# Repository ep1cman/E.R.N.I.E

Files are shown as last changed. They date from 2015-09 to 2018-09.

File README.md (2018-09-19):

About
=====

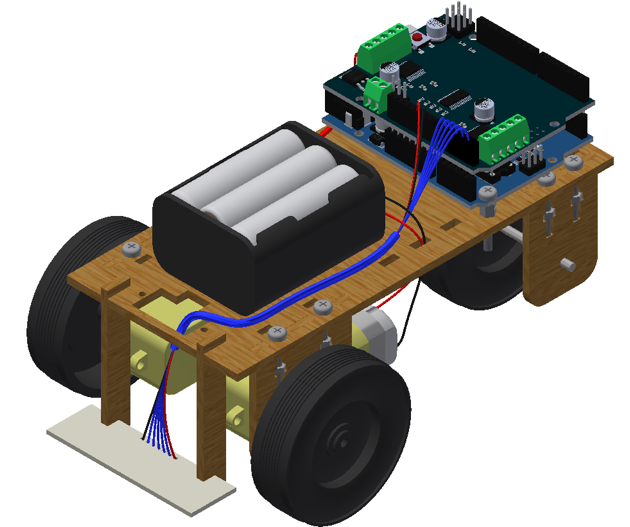
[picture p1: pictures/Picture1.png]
ERNIE Render 3D render of E.R.N.I.E


A few years ago [EARS](https://twitter.com/surreyears?lang=en) were asked by the University of Surrey to create a project for an event called [Headstart](http://www.etrust.org.uk/headstart/courses). During this week long event a group of sixth form students who are considering studying engineering at university have around 5 hours of lab sessions to complete a project.

E.R.N.I.E (EARS Robotic Navigator and Intrepid Explorer) was the project I came up with for the electronic engineering project. ERNIE is a very low cost line following robot that can be assembled and programmed by students with very little previous knowledge in electronics or programming.

Over the past few years the project has evolved to become (almost) fully re-usable by only requiring zip ties, screws and electrical tape to assemble. The only part that cannot be done again is the soldering of the PCB, but the assembled PCB can of course be re-used.

Notes for schools and people making their own
=============================================
Assembly instructions for building an E.R.N.I.E can be found [here](doc/assembly instructions.pdf).
While these are mostly complete they assume you have been given a ready made kit and don't include preparation details.
Additional notes for schools can be found [here](SCHOOLS.md).

If you are an individual wanting to make an E.R.N.I.E for yourself please read through the [kit preparation](SCHOOLS.md#kit-preparation) section on the schools page for details on the extra steps you will need to take. For individuals I can also offer free PCBs since I have quite a lot left over. All I ask is you cover the postage costs (won't be much because it can be sent as a small letter). Just drop me an email at sebastian.goscik@live.co.uk

Code examples
=============
Code examples for E.R.N.I.E are kept in a separate repository that can be found [here]()

Files
=====
 * __/BoM.pdf__ - Bill of Materials, contains a complete list of parts needed and where to buy them
 * __/Chassis v2.1.dxf__ - Chassis design for a laser cutter
 * __/Chassis v2.1.razorlab.svg__ - Same as above but ready to be sent straight to [Razorlab](http://razorlab.co.uk/) using their P1 size
 * __/README.md__ - This is the file you are now reading
 * __/SCHOOLS.md__ - Information on using E.R.N.I.E in schools e.g. kit preparation details
 * __/doc/assembly instructions.pdf__ - Instructions on how to assemble E.R.N.I.E (including diagrams)
 * __/doc/worksheet.pdf__ - Basic arduino and line following tutorial
 * __/doc/Sensor board - XXX.pdf__ - Schematic and PCB files in viewable form
 * __/license/XXX__ - Details about how this project is licensed, including who to email when you make changes or a production run
 * __/PCB/XXX__ - [Cadsoft EAGLE](http://www.cadsoftusa.com/) source files for the sensor board
 * __/src/3d/XXX__ - Autodesk Inventor source files that this project was made from
 * __/src/doc/XXX__ - Microsoft Word source files for the assembly instructions and worksheet
 * __/src/PCB/XXX__ - Cadsoft EAGLE source file for a panellised version of the pcb and the one used in the pcb pdf
 * __/src/PCB/gerbers (elecrow).zip__ - The gerber files sent to [Elecrow](http://www.elecrow.com/) to produce the PCBs
 * __/src/BoM.xlsx - Microsoft Excel source for the bill of materials

To Do
=====
There are a few extra things I would like to add to this project in the future if time permits:
 * 3D printed shroud for the IR sensors to minimise cross talk
 * 3D printed servo -> HC-SR04 mount
 * Add soldering instructions
 * add software setup instructions

If you manage to implement any of the above or something I haven't even considered please let me know!

Credit
======
The very first version of the E.R.N.I.E chassis was created with the help of my good friend [Revanth Adiga](https://uk.linkedin.com/pub/revanth-adiga/a7/94a/929)

CAD models used:
 * [Arduino by Andrew Whitham](https://grabcad.com/library/arduino-uno-r3-1)
 * [Motor Shield by mandrillon](https://grabcad.com/library/adafruit-motor-shield-v2-1)
 * [Battery Holder by Georgina Koffler](https://grabcad.com/library/6-aa-battery-pack)
 * [AA Battery by Cody Thurston](https://grabcad.com/library/energizer-aa-battery)

License
=======
Copyright S.Goscik 2015

The schematic, PCB and chassis designs and their respective documentation are Open Hardware and are licensed under the CERN OHL v. 1.2.
You may redistribute and modify this work under the terms of the CERN OHL v.1.2. (http://ohwr.org/cernohl). This work is distributed WITHOUT ANY EXPRESS OR IMPLIED WARRANTY, INCLUDING OF MERCHANTABILITY, SATISFACTORY QUALITY AND FITNESS FOR A PARTICULAR PURPOSE. Please see the CERN OHL v.1.2 for applicable conditions

There are only a few simple requirement that you must do under this license:

 * If you make any changes to the project please share them freely, under the same license.
 * Please list your changes in [CHANGES.TXT](license/CHANGES.TXT).
 * Please notify the people listed in [CONTRIB.TXT](license/CONTRIB.TXT) of your changes.
 * If you know how to use git and feel your change improve the project (e.g. fixing my spelling/grammar or updating the worksheet) please fork this repository and make a pull request of your changes.
 * If you produce any E.R.N.I.E kits (chassis or PCBs) please notify the people listed in [PRODUCT.TXT](license/PRODUCT.TXT).

If any of your e-mails fail to go through you don't need to worry about it. The reason I ask for these things is so that the people who have contributed to the project can see how it progresses and that it remains free for everyone.

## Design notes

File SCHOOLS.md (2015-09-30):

Using E.R.N.I.E in schools
==========================
E.R.N.I.E was designed from the very start to be used for education and therefore I have open sourced the project so any school can use and build upon it. If you wish to use E.R.N.I.E for teaching students here are a few recommendations from past experiences.

The kit can be assembled by 1-3 students. I find that two students to be the optimum amount. I would not recommend more than 3 students per group as there really isn't enough for them all to do simultaneously. The project requires around 5-7 hours to complete.

Learning Objective
------------------
As it stands E.R.N.I.E and its existing documentation aim to:
 * Teach how a line following robot works
 * Teach basic programming skills
 * Teach basic Arduino skills
 * Teach basic robot construction skills

There is also a lot of potential to widen the scope of this project. For example:
 * If your school has access to a laser cutter and time permits it, students could be allowed to watch their own kit be cut to learn about CAD/CAM.
 * The project also has the opportunity to utilise 3D printing to extend its features. It's likely this would need to be done in advance due to the time 3D printing requires, but students could be shown how 3D models are created. Then watch one start printing at the start of their session to see it complete at the end.
 * Two out of the three wheels need to have their hubs drilled out to 5mm. This can be done with a drill press set to very slow speeds due to the soft rubber material they are made of. This could be used to teach students fabrication skills.
 * Using ultra sonic sensor worksheets and examples for obstacle avoidance. *
 * For more advanced classes a PID controller could be implemented in software or hardware. *
 * The software could be written in low level C* rather than with Arduino libraries or even in Assembly
 * The Arduino and motor shield could be replaced by analogue electronics to teach basic Op-Amp theory *

\* denotes items which are in progress but I cannot guarantee when they will be complete.

License Details
===============
This project is licensed under the CERN open hardware license v1.2. This means you are free to use any of the files you find here however you see fit. There are only a few simple requirement that you must do under this license:

 * If you make any changes to the project please share them freely, under the same license.
 * Please list your changes in [CHANGES.TXT](license/CHANGES.TXT).
 * Please notify the people listed in [CONTRIB.TXT](license/CONTRIB.TXT) of your changes.
 * If you know how to use git and feel your change improve the project (e.g. fixing my spelling/grammar or updating the worksheet) please fork this repository and make a pull request of your changes.
 * If you produce any E.R.N.I.E kits (chassis or PCBs) please notify the people listed in [PRODUCT.TXT](license/PRODUCT.TXT).

If any of your e-mails fail to go through you don't need to worry about it. The reason I ask for these things is so that the people who have contributed to the project can see how it progresses and that it remains free for everyone.

Kit preparation
===============
Prior to students starting to build an E.R.N.I.E there are a few steps that need to be done in advance unless you have the time and want students to perform them. In this repository there is all file called BoM.xlsx (Bill of Materials). Said file contains a full list of what is required for the main chassis, the sensor board and the optional sonar sensor.

#### Laser cutting
The chassis can be laser cut from 3 materials each with their own pro's and con's:
 * __Acrylic__ - Looks good and is affordable but extremely brittle and easy to break.
 * __Plywood__ - Cheap, strong and can easily be modified but some people think it looks less attractive.
 * __Polycarbonate__ - More expensive than acrylic but not brittle.
I personally would recommend using plywood as it is more robust and can easily be hacked by students wanting to modify their robots.

If you do not have access to a laser cutter there are several companies who offer laser cutting services for very reasonable prices online. I have included a ready made [file](Chassis v2.1.razorlab.svg) for [Razorlab](http://www.razorlab.co.uk/). The design fits onto their P1 size sheets and will set you back ~£11.50 for a plywood E.R.N.I.E, although I am sure in bulk the price would decrease. Be sure to use 3mm thick material.

#### Wheels
Each kit needs 3 wheels, two of which need to have their hub enlarged to 5mm. This can be done very easily on a drill press running on a slow speed or by hand with a drill bit.

#### PCBs
I highly recommend getting professionally manufactured PCBs from one of the many Chinese PCB fab houses. I used [Elecrow](http://elecrow.com) and got 50 boards produced for £22.57 (45p a board!). If you would like to recreate the exact boards I got made you can simply visit [this page](http://www.elecrow.com/10pcs-2-layer-pcb-p-1175.html) and enter the following settings:
 * __Layer__ - 2
 * __PCB Thickness__ - 1.6mm
 * __Copper Weight__ - 1oz 35um
 * __PCB Size__ - 10cm Max * 10cm Max
 * __PCB Color__ - Black
 * __Suface Finish__ - Hasl (lead free)
 * __PCB Stencil__ - NO Stencil
 * __Panelizing__ - 2-5 copies
 * __Lead time__ - Shipped in 4 to 7 days
The zip file you need to attach can be found [here](src/PCB/gerbers (elecrow).zip)

#### Packaging
I find Tesco zip lock freezer bags are the perfect size for the E.R.N.I.E kit. I would advise against packing the six AA batteries with the rest of the kit to prevent them getting shorted by components.

When packing the IR LEDs and IR photodiodes be very careful not to mix them up. Either bag the two individually or use tape to keep them together and label them. The two are __VERY__ difficult to distinguish. On a side note, mobile phone cameras are an extremely good way to test if the IR LEDs are working. Most mobile cameras do not fully filter out IR light and they should appear white/blueish when illuminated.

#### Spare parts
I would highly recommend getting spares of the following components:
 * __IR LED/Photodiodes__ - Inevitably someone will solder an LED into a photodiode slot or the wrong way around. Its easier to use a fresh one than try salvage a used one.
 * __Sensor Holders__ - If these are made from acrylic they can be very easy to break if too much force is applied to them.
 * __Nuts__ - very easy to loose and you can buy them in large quantities very cheaply.

#### Software
The arduino software runs well on all major operating systems but does require administrator privileges on windows to install drivers. If the students will not be using accounts with administrator privileges (as is the case in most schools) please ensure that you plug an arduino into every USB port they might use on the PCs. Windows will then proceed to install drivers which will not need to be done again by the students.

The worksheet has been written using version 1.6.5 of the arduino IDE. With only minor changes (the library installation) it can work with much older versions. It may also be the case that future arduino IDE releases might slightly change the steps shown in the worksheet but these are unlikely to be major. If this is the case let me know and I will update the worksheet.

Students also require internet access to be able to install the adafruit motor shield v1 library, if this is not possible you will need to go ahead and pre-install the library on their machines. Instructions on doing this can be found [here](https://learn.adafruit.com/adafruit-motor-shield/library-install) (please ignore the message about v2 at the top of this page).

#### Testing
If you opt for using chinese clone arduinos and the adafruit motor shields (which dramatically decreases the cost of the kit). I would highly recommend testing the hardware before giving it to students and possibly ordering a spare of each. I have encountered some shoddy soldering on a motor shield in the past that had prevent it from working.

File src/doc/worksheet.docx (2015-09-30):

# Project Aims

Over the course of the next few hours you will be learning how to make a line following robot. The aims of this project are:

- Learn how a line following robot works
- Learn basic programming skills
- Learn basic Arduino skills
- Construct a line following robot

# Pack Contents

1x Arduino 1x Motor shield 1x 9v battery clip 1x 6xAA battery holder 6x AA Batteries 1x Base plate 2x Motor mounts 2x Rear axle mounts 2x Sensor holders 2x Geared motors 1x Axle shaft | 3x Wheels 1x Long zip tie 8x Short zip ties 10x 20mm M3 bolts 4x 30mm M3 bolts 17x M3 nuts 1x Senor PCB 5x IR LEDs 5x IR Photodiodes 5x 330 Ohm resistors (Orange Orange Brown) 5x 10k Ohm resistors (Brown Black Red)

What is a line following robot and how does it work?

As you might have already guessed, a line follower is a robot that follows a marked line. In this project the goal will be to design a robot that can navigate a track with multiple turns made from black electrical tape. The way the robot will be able to detect its position relative to the track will be via an array of 3-5 Infrared (IR) reflectance sensors. These sensors consist of two parts, an IR LED and an IR photodiode. The LED emits light, which is then reflected by the surface into the photodiode:

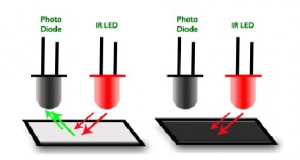
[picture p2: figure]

Depending on the colour of the surface the amount of light reflected will vary. In our case we will be using a white surface with a black line. As can be seen in the previous diagram, the black surface absorbs all the IR light while the white reflects it all. The photodiode will produce a current proportional to the amount of IR light it receives. Using this we can build the following circuit to detect whether the sensor is above a white or black surface:

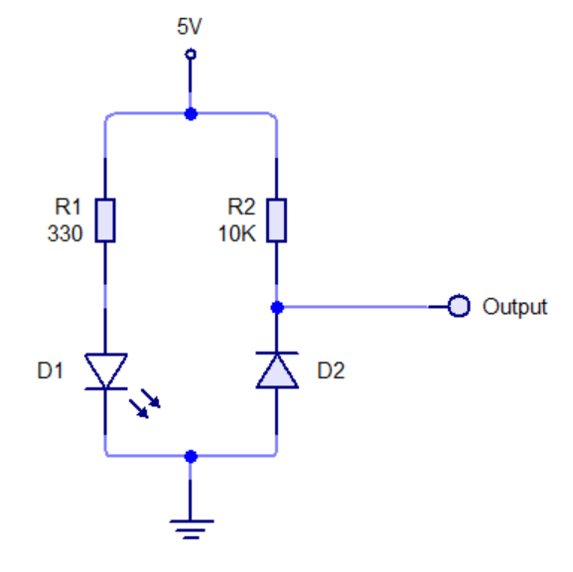
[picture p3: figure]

While ideally the black line will absorb all IR emitted by the LED, in reality this isn’t the case. The reflected IR and ambient light will mean that the sensor will output a small amount of current even on the black line. It will be your task to figure out how to solve this in your code later on.

The minimum number of sensors needed to successfully follow a line is two. One on either side of the track (you can get away with one sensor but its unreliable). Using two sensors tends to lead to a lot of wobbling so it is recommended to use three, one on the line and one either side.

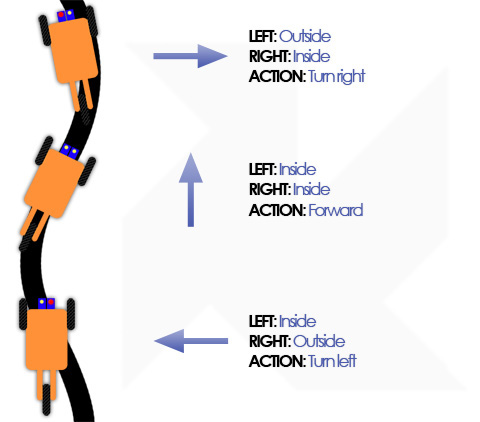
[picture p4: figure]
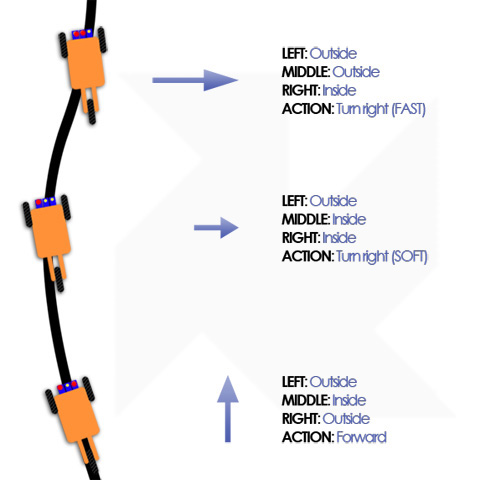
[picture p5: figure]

Once you have an array of sensors you can then steer the robot based on how much light each one receives.

Writing your first Arduino program

1. On the desktop you should find the following icon, double click it to open the Arduino software:
2. You should then have following window appear:

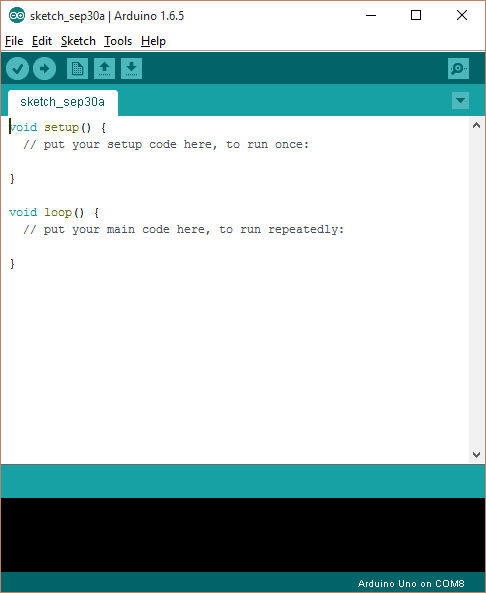
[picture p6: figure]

Please take note of the two functions called “setup()” and “loop()”. The setup function is run once when the Arduino starts, after this the loop function runs indefinitely. Also Arduino programs are called sketches.

3. If you look at the Arduino pinout diagram provided, you will notice it has 14 digital pins numbered 0 to 13. These pins can be set as either inputs or outputs. In this example we will set pin 13 to an output. Pin 13 is connected to an on-board LED. To do this simply add the following line of code into the setup function:

pinMode(13,OUTPUT);

Code is case sensitive so make sure you copy it exactly as shown.

4. Now that pin 13 is set as an output, we can either output “HIGH” or “LOW”. Setting a pin HIGH will make it output 5 volts, while setting a pin LOW will make it output 0 volts.

To change the state of a pin we use the “digitalWrite” function. In this example we will blink the LED connected to pin 13 once a second (1000 milliseconds). Type the following code into the loop function:

digitalWrite(13, HIGH);

delay(1000);

digitalWrite(13, LOW);

delay(1000);

5. Now that we have written our code it’s time to upload it to the Arduino. The first thing we need to do is to make sure the Arduino IDE is set to the correct board type. To do this go to Tools>Board and ensure Arduino Uno is selected:

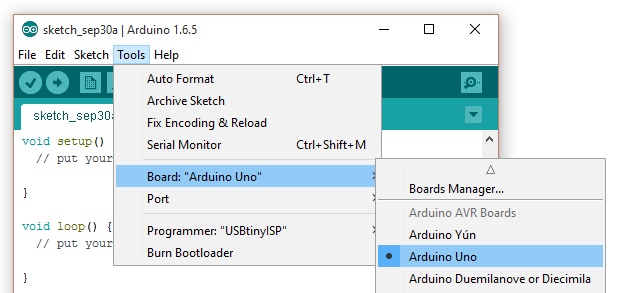
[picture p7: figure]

Next we need to ensure the Arduino IDE is using the correct COM port. Depending on your PC configuration there may be more than one. The COM port can be changed by going to Tools>Port. In the latest version of the Arduino IDE it should show you which COM port is the Arduino (If you have any problems just ask a demonstrator for help).

6. The last step is to actually upload the code to the Arduino. This can be done by pressing the arrow button at the top of the Arduino IDE:

If everything has been successful, the bottom part of the window should say “Done uploading.” (If you get an error call over a demonstrator for assistance).

7. Once the uploading is complete you should notice an LED near the USB plug blinking roughly once a second.
8. See if you can change the speed at which it blinks, or make the Arduino blink a pattern.

Reading analog inputs (You will need to have soldered your PCB to complete this section)

In the previous section we used the digital I/O (Input/Output) pins as outputs to blink an LED. In your robot these outputs will be used to drive motors. The next thing we need to learn is how use the analog inputs. In electronics you will find two types of signals, digital and analog:

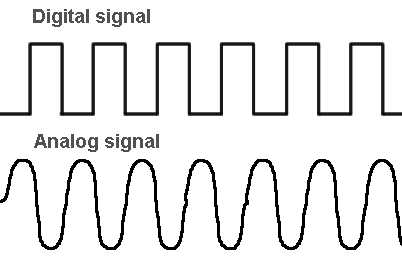
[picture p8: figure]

Digital signals have only two states: HIGH/1 or LOW/0, information is sent as a series of 0s and 1s in digital signals. Analog signals on the other hand can have any number of states, therefore they cannot be expressed using only two values. The Arduino has special inputs for reading analog signals. These inputs have an analog to digital convert attached to them. The converter will turn a signal in the range of 0 volts to 5 volts into a value between 0 and 1024.

1. Once you have built the circuit open the Arduino IDE and go to: File>Examples>03.Analog>AnalogInOutSerial

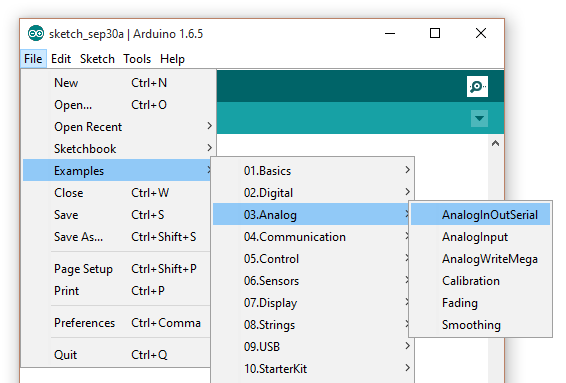
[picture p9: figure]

This file contains some ready made code to allow you to send data to the PC.

2. To read analog inputs we need to use the analogRead() function. This function takes an analog pin as a parameter. If you look on the Arduino, you will notice the analog pins are labelled A0 to A5. You can see in the file we just open this is done on the following line:

sensorValue = analogRead(analogInPin);

Notice there are two things special about this, firstly we did not have to set the pin mode, this is because all analog pins are input only. Secondly we assigned the value to a variable called “sensorValue”. Variables are used in code when you wish to save a value to later manipulate or recall it. In this case we declared sensorValue as an “int” at the top of the code, this means we expect sensorValue to be an integer (whole number).

3. Next we will need to connect one of the IR sensors to the Arduino. Connect the power and ground connections from the sensor board to the corresponding pins on the Arduino. Along with one of the sensor cables to an analog input A0 (a pinout of the Arduino can be found at the end of this guide).
4. Now upload your code to the Arduino.
5. Once the uploading has successfully completed, you will need to open the serial monitor. This is a window that will allow you to see data the Arduino is sending back to the PC. It can be accessed by clicking the following icon in the top right of the Arduino IDE:

When this has opened you should see something like this (ignore the output value):

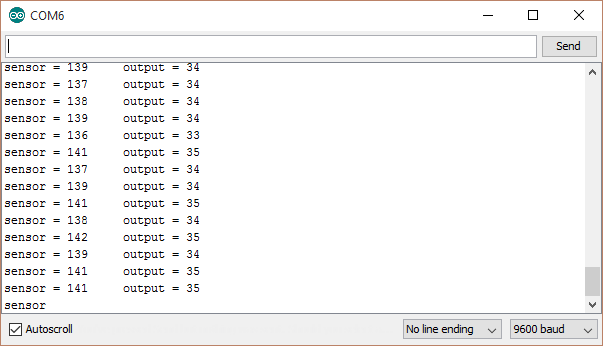
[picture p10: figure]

6. Now try passing the line test sheet you were given over the sensor, you should notice the values change
7. Take note of the sensor values you get when you hold the sheet about 1cm from the sensor

White: _____________________________________________

Black: _____________________________________________

Conditional branches

Now that we are able to get an input, you may be wondering how we can react to the inputs. This can be done using by conditional branching, the simplest of which is an if statement. An if statement is formatted as follows:

if(condition)

{

//Code that will run if condition is true

}

else if(otherCondition)

{

//Code that will run if condition was false but otherCondition is true

}

else

{

//Code that will run if both condition and otherCondition are false

}

The condition can be comprised of many different logical operators below is a table of all the ones you might need:

Operator | Name | Description
> | Greater than | True when the left is greater than the right
< | Less that | True when the left is less than the right
== | Equals | True when the numbers are equal
|| | OR | True when either condition is true
&& | AND | True when both conditions are true

E.g. if(sensorValue>300)

We will now modify the code from the previous section, to light the on-board LED depending on if the sensor is over the track or not.

1. Add the following code below the sensorValue = analogRead(analogInPin); line

if(sensorValue>VALUE)

{

}

else

{

}

Change VALUE to be a number somewhere in between the two values you wrote down earlier.

2. Now adding the code you wrote in part one into the if statement, make the on board LED light up when the track is over the sensor (Don’t forget to set the pinMode in the setup function!).

Motor Shield

Before we can start using the motor shields, we have to install an Arduino library for it. A Library is a set of ready made code that will make using the motor shield easier.

1. First we need to open the Library manager by going to Sketch>Include Library>Manage Libraries…

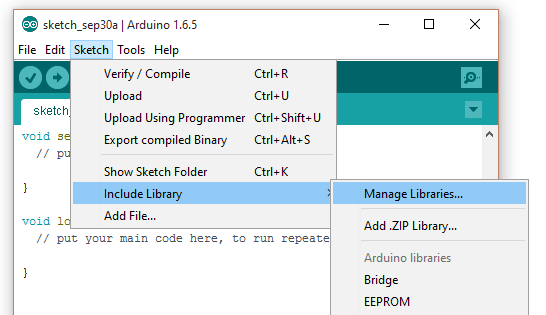
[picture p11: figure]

2. You should then have following window appear:

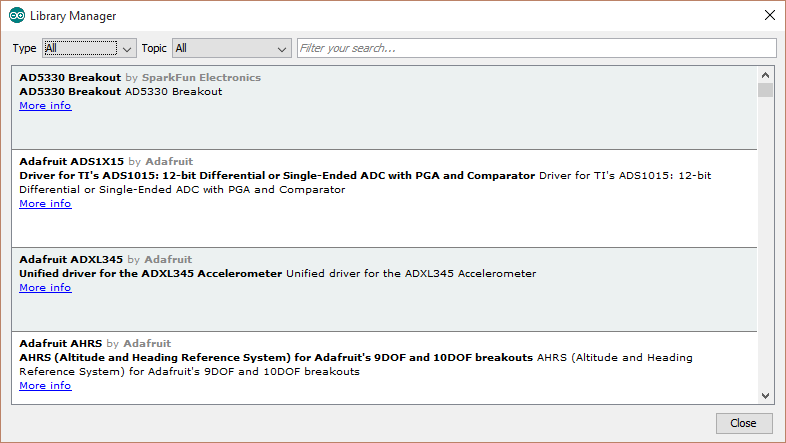
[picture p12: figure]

3. In the search box type in “Adafruit motor shield v1” and you should see:

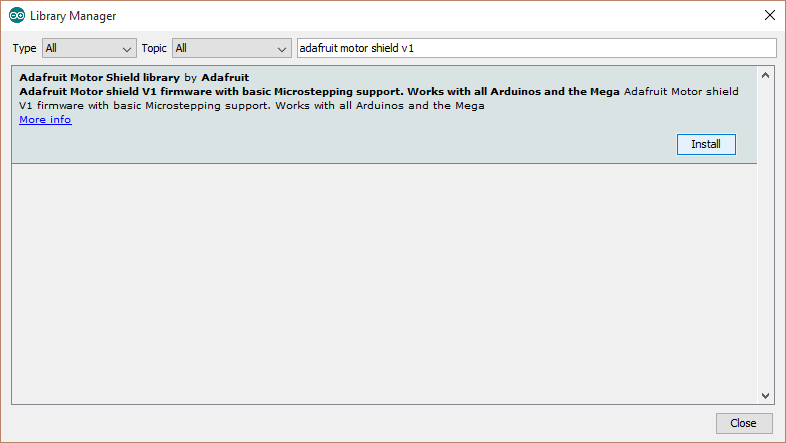
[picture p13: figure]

4. Click the install button to install the library onto your computer

Once you have the motor shield library installed, please fully close and re-open the Arduino IDE to ensure it will work correctly. Once you have a fresh Arduino sketch open, add the following line as the first line in your sketch:

#include <AFMotor.h>

This line will allow us to use the functions provided in the motor shield library. After this line we will need to add the following code:

AF_DCMotor motor(2);

This creates an object called motor that will allows us to control motor 2. If you look on your motor shield you will see pairs of terminals along the edges labelled M1, M2, M3 and M4.

In this example the code will control M2. Now we need to set a speed for the motor by adding the following line into the setup function:

motor.setSpeed(255);

The motor speed can be varied in 255 increments with 0 being off and 255 being full speed. For this project there is no need to vary the speed of the motors unless you want to get fancy. Now in our loop function we simply need to tell the motor shield how we want our motor to move. There are three options: FORWARD, BACKWARD or RELEASE. To set the direction of the motor simply use the following code:

motor.run(FORWARD);

See if you can write code to alternate the direction of the motor once every second. After that see if you can control two motors at once!

Note: When using a second motor remember to change the name of the second motor e.g.

AF_DCMotor left(1);

Line following robot

By using what you have learnt in the previous sections, you should now be able to program a simple line following robot. You will need to read in values from all 5 sensors and then decide how the robot should react. (If you have any queries or you code isn’t compiling and you can’t figure out why just ask for help from one you your demonstrators). Good luck and most importantly, have fun!

Pinouts

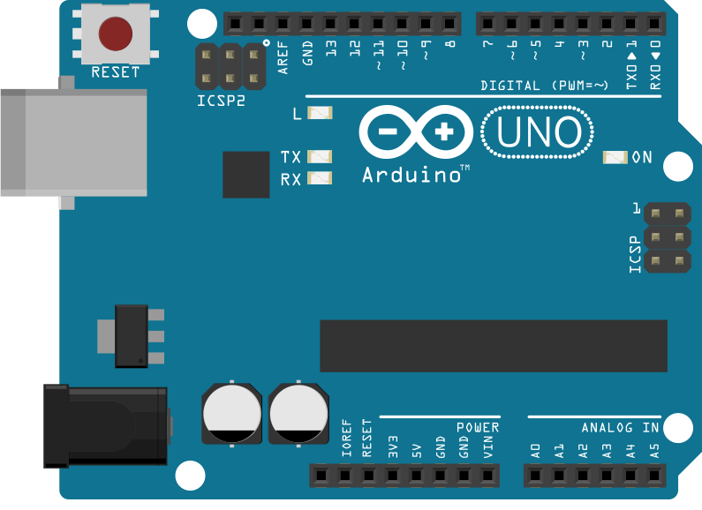
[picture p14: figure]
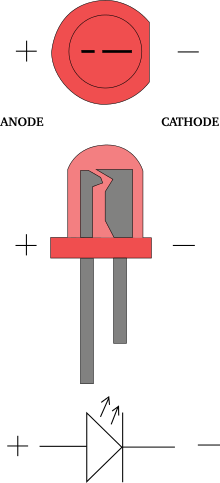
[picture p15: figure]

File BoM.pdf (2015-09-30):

Description | Amount Cost | Total | Supplier | Order
Code | Comment
Main

Robot

Chassis | £
25.4404 | This

is

including

many

spares.

It's

highly

likely

you

already

own

some

of

these

items

too
A4

acrylic

3mm | 1 £

3.1000 £

3.1000 eBay | 201121042564 More

aesthetically

pleasing
A4

plywood

3mm | 1 £

3.4900 £

3.4900 eBay | 252056858061 Preferred

ito

acrylic:

Does

not

break

as

easily

as

acrylic

which

is

very

brittle
20mm

M3

screw | 10 £

0.0158 £

1.5800 Rapid

Electronics | 33-‐2320 Pack

of

100
30mm

M3

screw | 4 £

0.3300 £

1.6500 eBay | 221265564237 Pack

of

5
M3
nut | 17 £

0.0065 £

0.6500 Rapid

Electronics | 33-‐1710 Pack

of

100
DC

geared

motor | 2 £

1.8100 £

3.6200 Rapid

Electronics | 37-‐1217
25mm

rubber

wheel | 3 £

0.8550 £

3.4200 Rapid

Electronics | 37-‐1320 Pack

of

4
2x75mm

steel

shaft | 1 £

0.0199 £

0.9936 Rapid

Electronics | 37-‐0350 Pack

of

50
9v

battery

clip | 1
6xAA

battery

holder | 1
AA
Battery | 6 £

0.3828 £

2.2968 Rapid

Electronics | 18-‐1452
Arduino | 1 £

2.5600 £

2.5600 eBay | 221802708989 The

price

is

for

a

cheap

Chinese

clone.

Genuine

ones

are

£25
Adafruit

motor

shield | 1 £

1.9500 £

1.9500 eBay | 141675106854 The

price

is

for

a

cheap

Chinese

clone.

Adafruit

style

motor

shield

preferred

as

it

allows

for

servos
Cable

tie

(L=200mm

W=4.6mm) | 1 £

0.0087 £

0.8700 Rapid

Electronics | 04-‐0754 Pack

of

100
Tape | 1 £

0.6600 £

0.6600 Rapid

Electronics | 87-‐1552 Black

electrical

tape

works

best
Sensor
PCB | | £

12.7132 This

is

including

many

spares.
PCB | 1 £

6.5000 £

6.5000 Chinese

| | | PCB
fab | If

you

are

interested

in

some

of

these

contact

me,

I

have

many

left

over
IR
LED | 5 £

0.1104 £

0.5520 Rapid

Electronics | 58-‐2006
IR
phototransistor | 5 £

0.1104 £

0.5520 Rapid

Electronics | 58-‐2005
330

Ohm

resistor | 5 £

0.0074 £

0.7416 Rapid

Electronics | 62-‐0358 Pack

of

100
10

Kohm

resistor | 5 £

0.0074 £

0.7416 Rapid

Electronics | 62-‐0394 Pack

of

100
7

Pin

0.1"

header | 1 £

2.1500 £

2.1500 eBay | 400858209683
Male

to

Female

jumper

wire | 7 £

0.0248 £

0.9900 eBay | 111651703549
Small

cable

tie

(L=80mm

W=2.4mm) | 2 £

0.0049 £

0.4860 Rapid

Electronics | 04-‐0630 Pack

of

100
Obstacle
sensor | | £
7.3800 | This

is

including

many

spares.
Servo | 1 £

2.0400 £

2.0400 eBay | 380661514413
HC-‐SR04 | 1 £

2.1200 £

2.1200 eBay | 400795830076
HC-‐SR04

servo

adapter | 1 £

0.9900 £

0.9900 eBay | 141741597378 3D

printable
10mm

M2

screw | 2 £

0.0118 £

1.1800 Rapid

Electronics | 33-‐2210 Pack

of

100,

Can

be

used

to

mount

Arduino

properly
m2
nut | 2 £

0.0105 £

1.0500 Rapid

Electronics | 33-‐1725 Pack

of

100

They

can

be

replaced

with

solid

core

wire

£

1.7000 £

1.7000 eBay | 121748057634 Both

Together

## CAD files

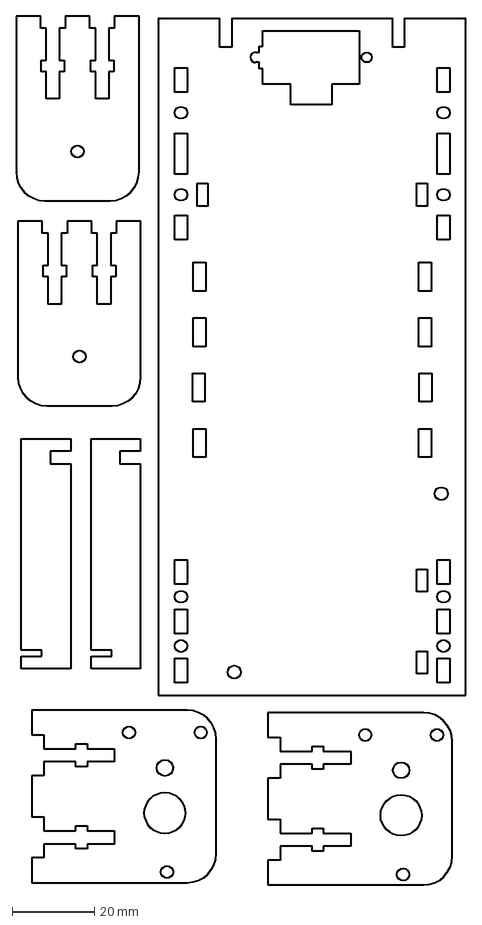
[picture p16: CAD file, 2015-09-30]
Chassis v2.1.dxf
109.7 x 211.8 mm

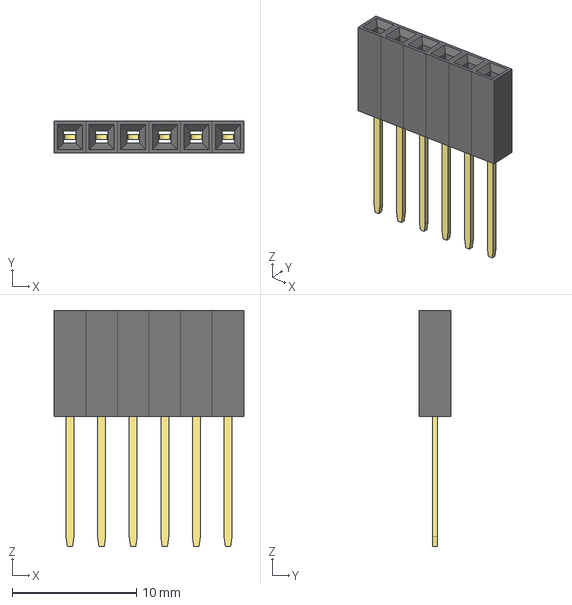
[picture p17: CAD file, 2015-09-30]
src/3D/Imported Components/motor shield/SIL_Socket06_.stp
15.2 x 2.54 x 19.0 mm

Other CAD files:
src/3D/laser cut.dwg
src/3D/3mm nut.ipt
src/3D/6AA Battery Pack.ipt
src/3D/Assembly Diagrams/step 1.ipn
src/3D/Assembly Diagrams/step 1b.iam
src/3D/Assembly Diagrams/step 2.ipn
src/3D/Assembly Diagrams/step 3.ipn
src/3D/Assembly Diagrams/step 4.ipn
src/3D/Assembly Diagrams/step 5.ipn
src/3D/Assembly1.iam
src/3D/Assembly1/AIP/Cable and Harness/Assembly1.Harness1.iam
src/3D/Assembly1/AIP/Cable and Harness/Assembly1.Harness1.ipt
src/3D/Assembly1/AIP/Cable and Harness/Assembly1.Harness2.iam
src/3D/Assembly1/AIP/Cable and Harness/Assembly1.Harness2.ipt
src/3D/Assembly1/AIP/Cable and Harness/Assembly1.Harness3.iam
src/3D/Assembly1/AIP/Cable and Harness/Assembly1.Harness3.ipt
src/3D/Assembly1/AIP/Cable and Harness/OldVersions/Assembly1.Harness3.0001.ipt
src/3D/Assembly1/AIP/Cable and Harness/OldVersions/Assembly1.Harness3.0002.iam
src/3D/BatteryDone.ipt
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

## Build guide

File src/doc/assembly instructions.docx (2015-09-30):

# Assembly Instructions

# Pack Contents

1x Arduino 1x Motor shield 1x 9v battery clip 1x 6xAA battery holder 6x AA Batteries 1x Base plate 2x Motor mounts 2x Rear axle mounts 2x Sensor holders 2x Geared motors 1x Axle shaft | 3x Wheels 1x Long zip tie 8x Short zip ties 10x 20mm M3 bolts 4x 30mm M3 bolts 17x M3 nuts 1x Senor PCB 5x IR LEDs 5x IR Photodiodes 5x 330 Ohm resistors (Orange Orange Brown) 5x 10k Ohm resistors (Brown Black Red)

In addition to this you will need four ~20cm lengths of stranded wire for the motors and seven ~20cm lengths of solid core wire for the sensor PCB.

1. Solder stranded wire onto the motors. The wires should be around 20cm long. If in doubt, cut the wire longer, you can always cut it down later.
2. Attach the motor to the mount using the (longer) 30mm screws:

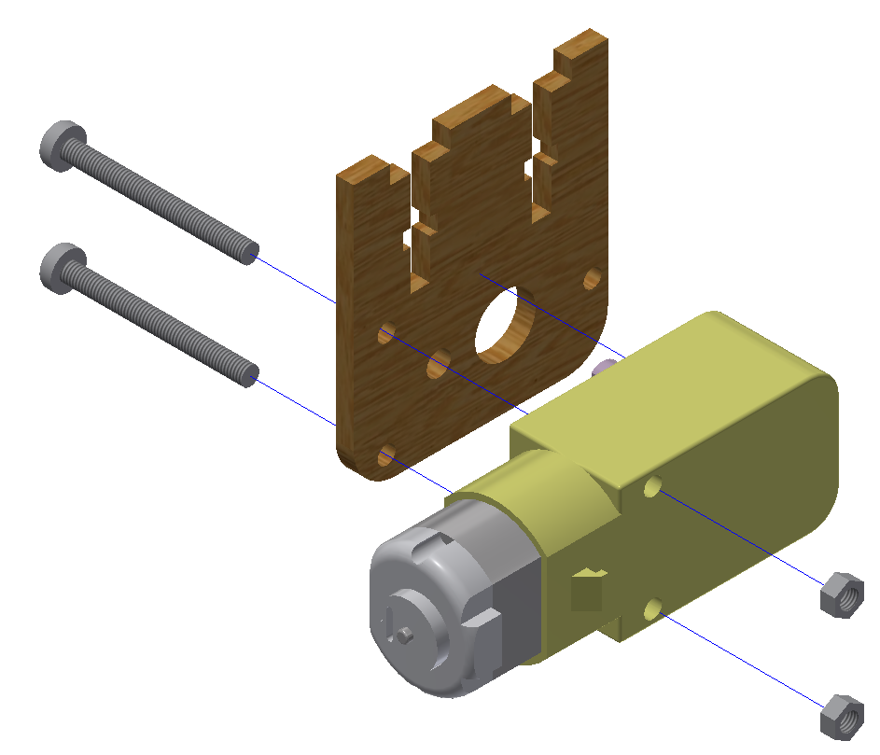
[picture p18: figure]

Repeat this for the second motor but this time mirrored. The end result should look like this:

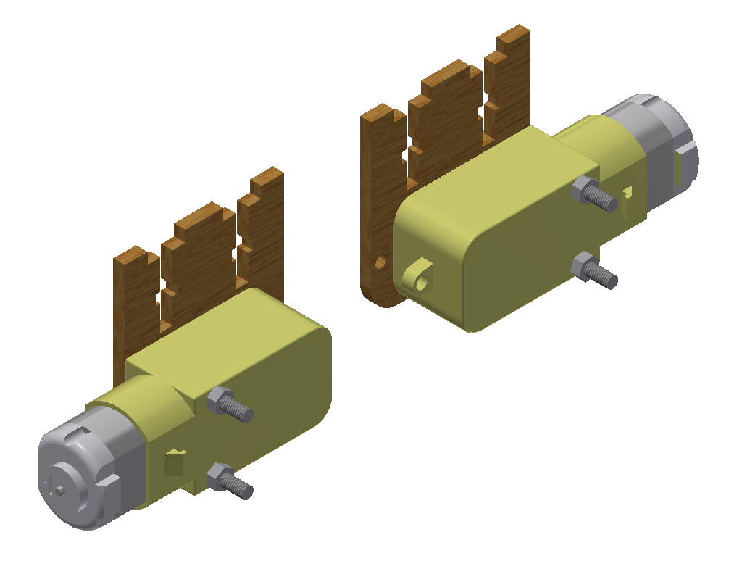
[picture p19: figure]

3. Attach the motor and axle mounts to the base plate using the 20mm screws:

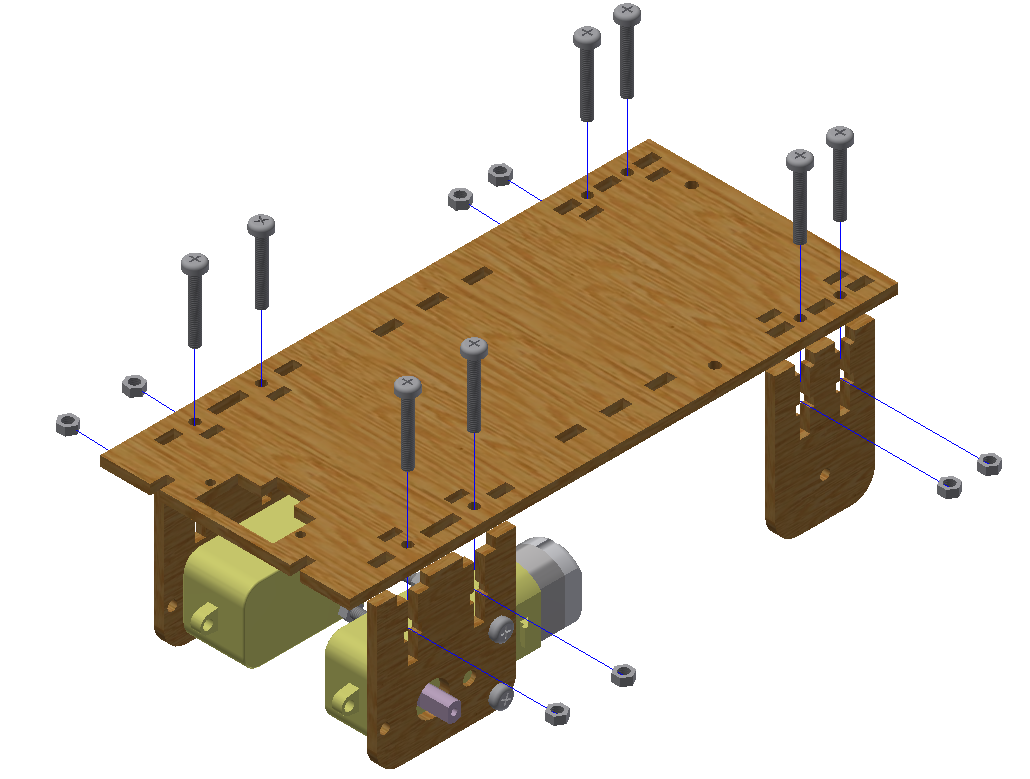
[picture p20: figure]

NOTE: Do not over tighten the screws. Acrylic is a very brittle plastic and will crack easily if too much force is applied. Don’t worry if the mounts have a little bit of movement in them, this will not affect the robot’s functionality.

4. Mount the Arduino to the base plate using 2 nuts as a spacer. Note that the front screw goes from the bottom and the back screw from the top:

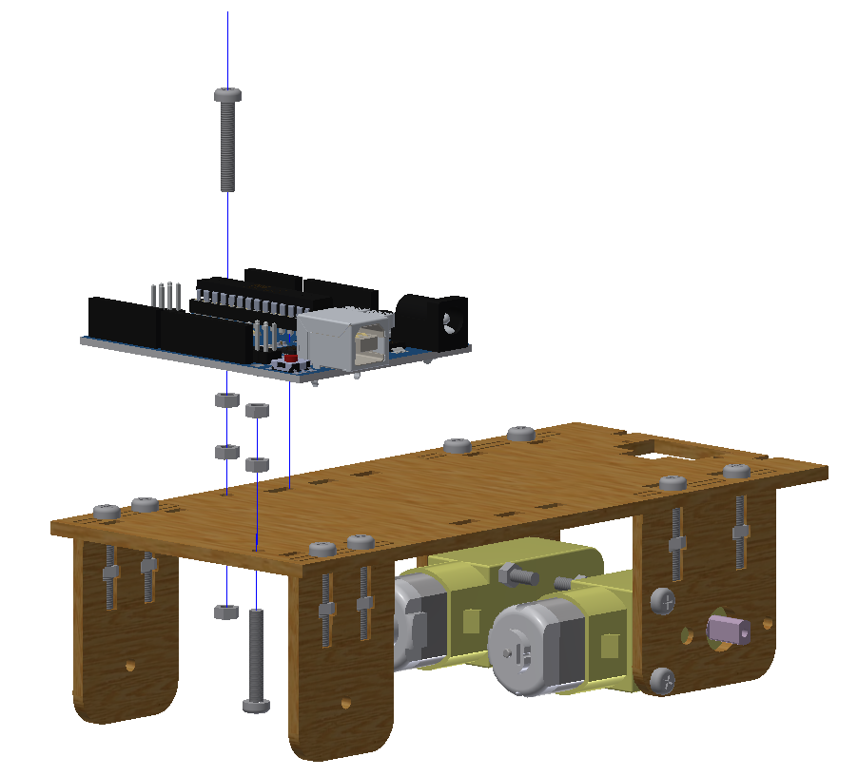
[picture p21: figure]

5. Apply electrical tape around the rear wheel (the one with the smaller hole). This is so that the back wheel can easily slide around when the robot turns.
6. Attach the wheels to the robot:

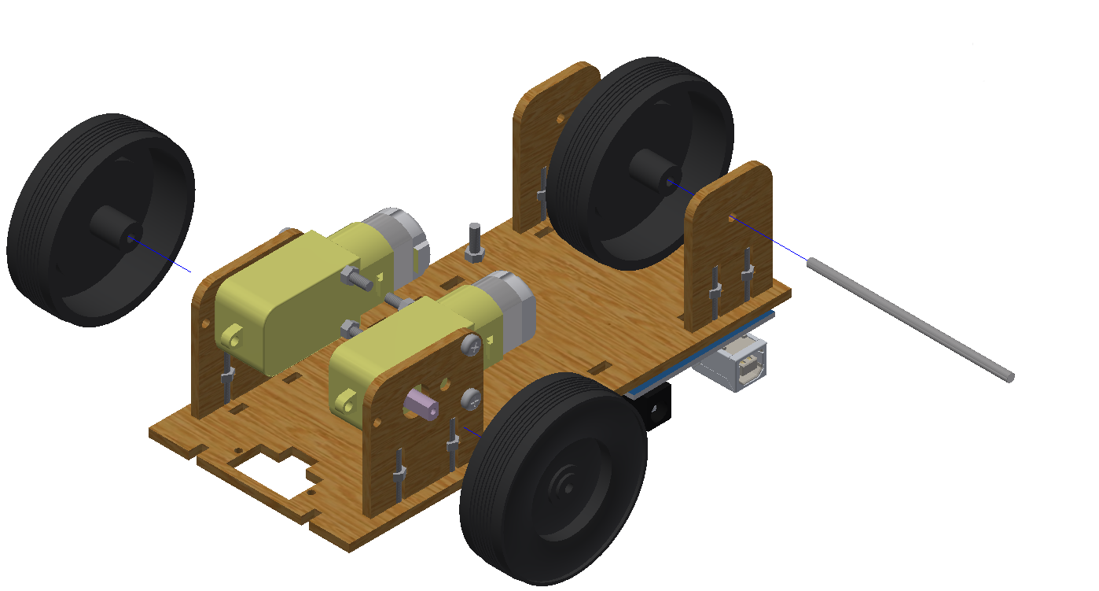
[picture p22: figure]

7. You will find that the rear axle easily slips out of its mounts. To fix this simply wrap a little bit of electrical tape around the axle so it cannot slide around.
8. To prevent the front wheels from falling off, use the short zip ties to tighten the wheels onto the motors. If you find that the wheels still fall off, remove the wheels, place hot glue into the hole and reattach them.
9. Plug in the motor shield and wire up the two motors:

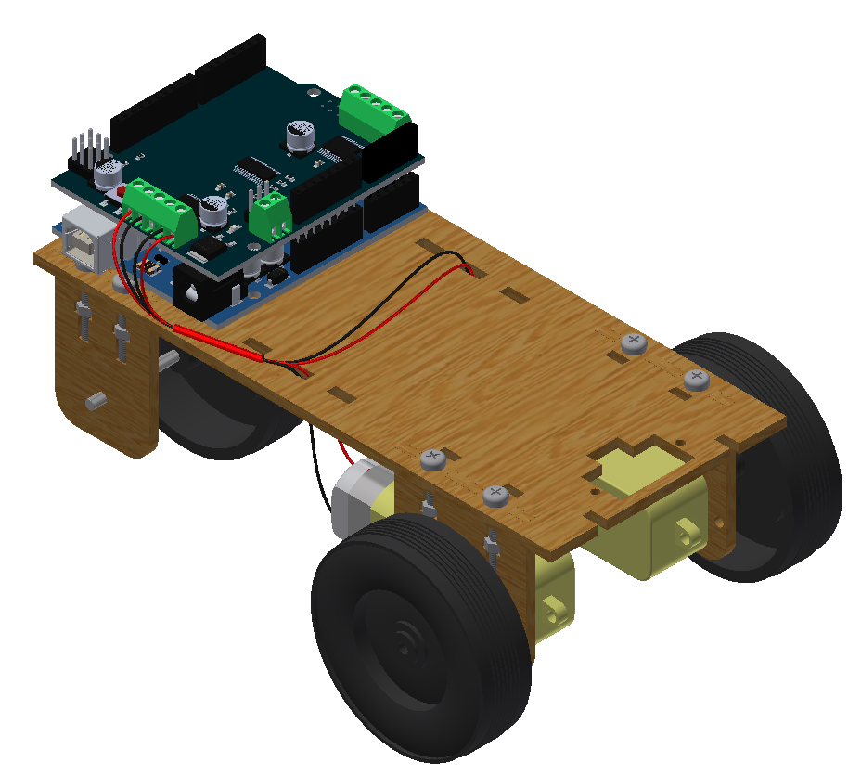
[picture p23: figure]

10. Attach Sensor holders:

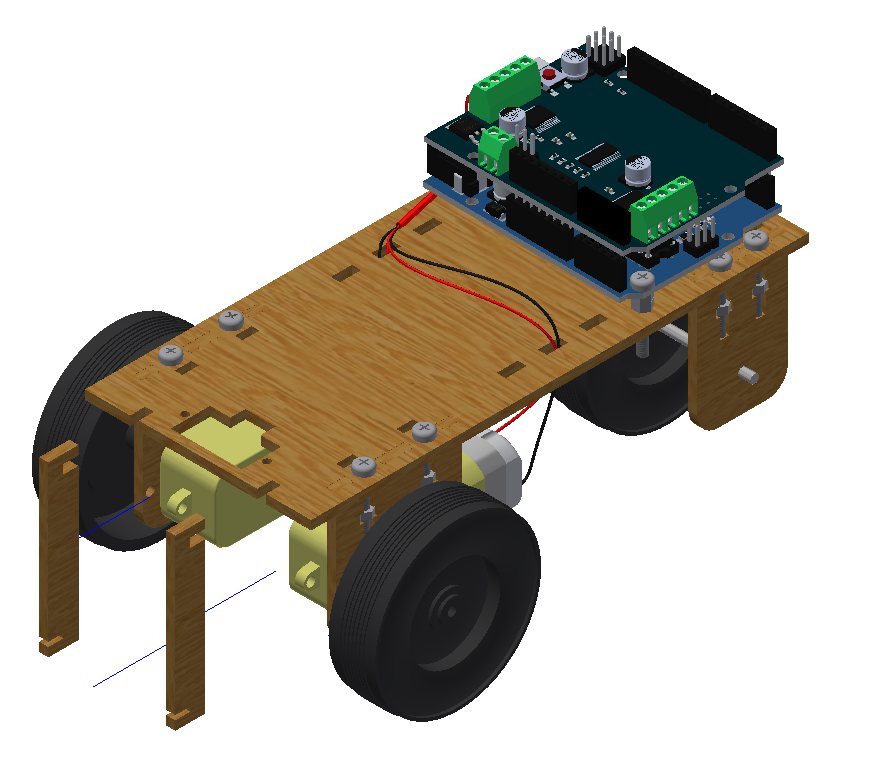
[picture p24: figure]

11. If the sensor holders a loose, use small zip ties to attach them to the motors.
12. Attach the senor PCB:

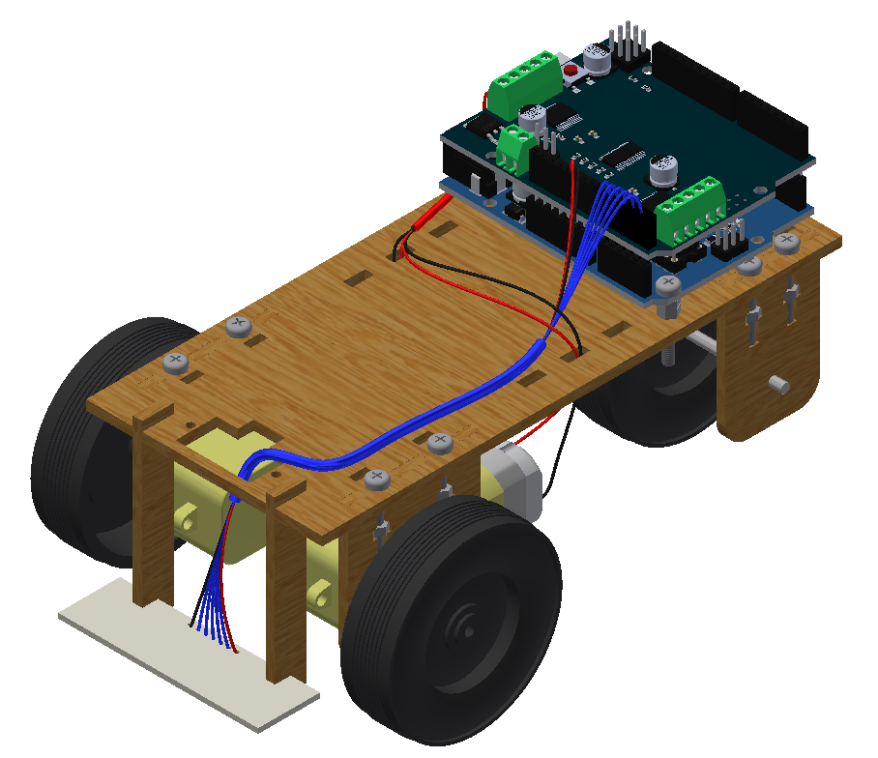
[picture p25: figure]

A pinout for the sensor PCB can be found in the soldering instructions. Just match that to the labels on the side of the Arduino.

13. Attach the battery pack (with the 6 AA batteries inserted) using the two large zip ties. One will need to go in from the top and the other from the bottom before you join them together:

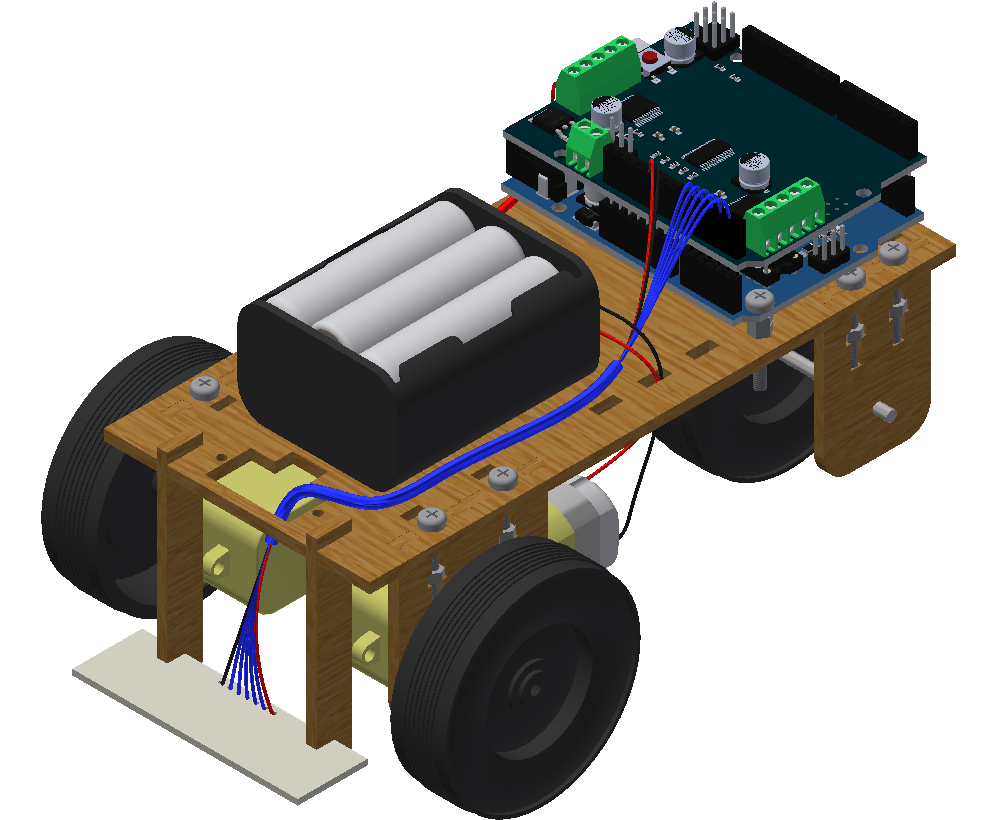
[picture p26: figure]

14. Connect the battery pack to the motor shield using the 9v battery connector. The red wire goes to the M+ terminal and the black wire goes to the GND terminal.

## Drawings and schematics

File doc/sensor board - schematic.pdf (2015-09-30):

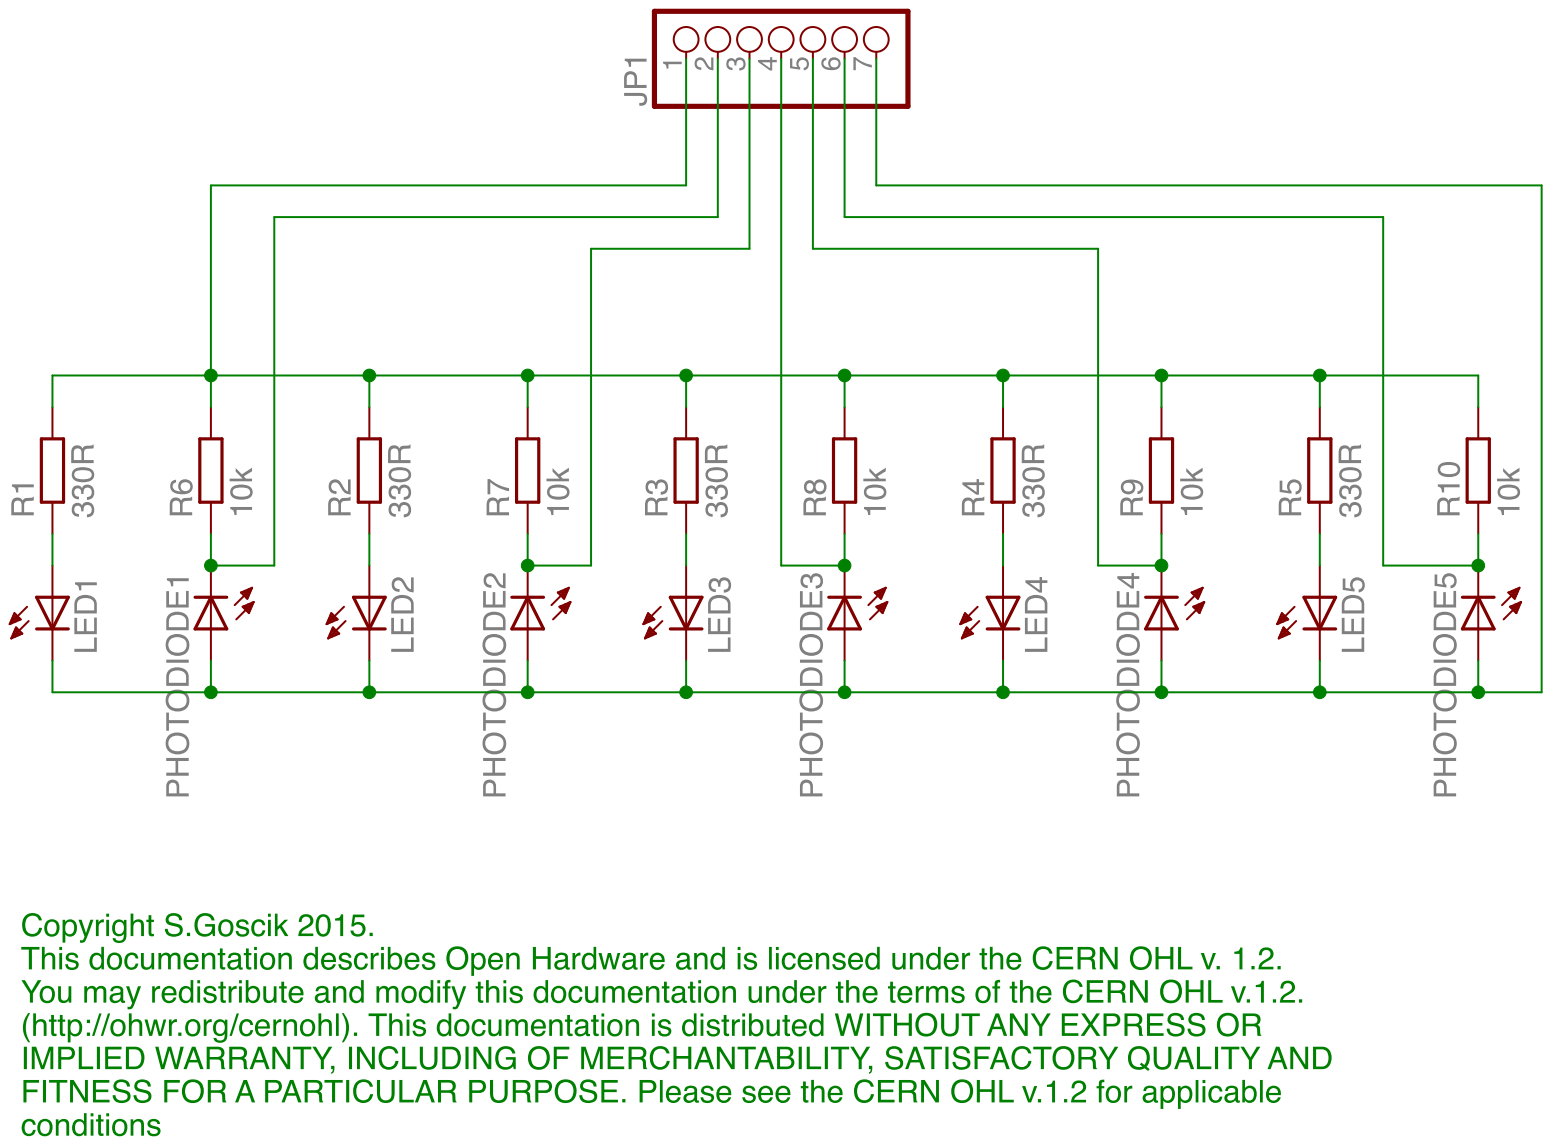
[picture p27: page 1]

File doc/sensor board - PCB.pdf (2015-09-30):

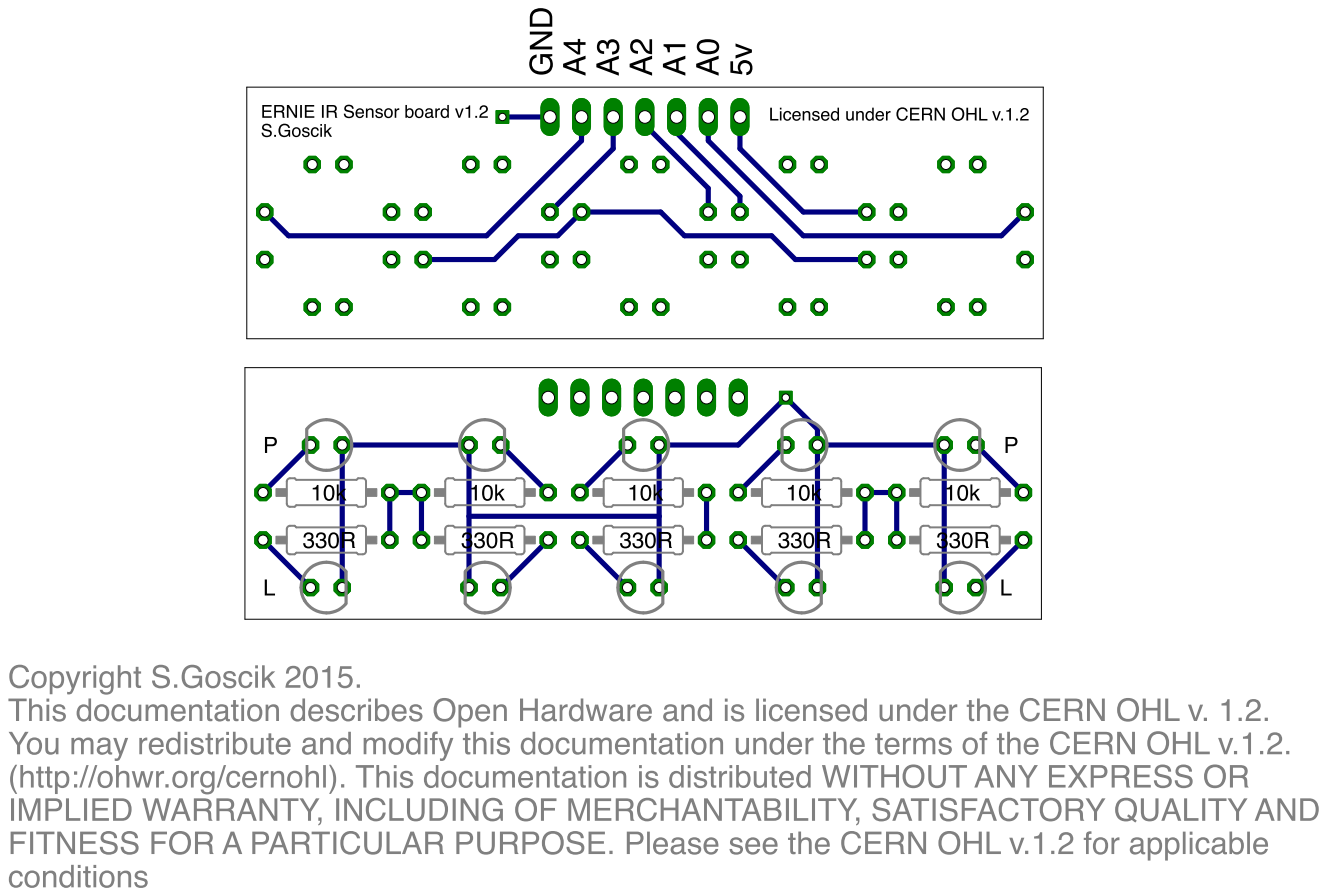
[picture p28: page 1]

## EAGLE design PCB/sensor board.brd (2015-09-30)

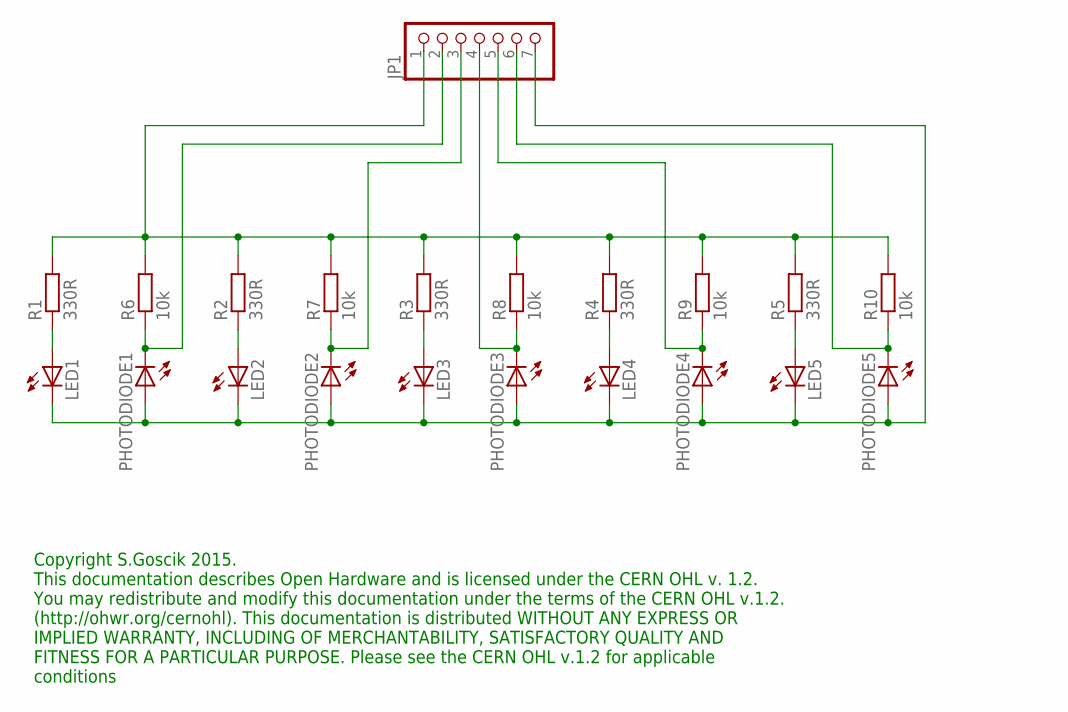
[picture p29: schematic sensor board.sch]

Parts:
JP1: PINHD-1X7; 1X07
LED1, LED2, LED3, LED4, LED5: LED3MM
PHOTODIODE1, PHOTODIODE2, PHOTODIODE3, PHOTODIODE4, PHOTODIODE5: LED3MM
R1, R2, R3, R4, R5: 330R; 0207/10
R6, R7, R8, R9, R10: 10k; 0207/10

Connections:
unnamed: LED1.A, R1.1
unnamed: LED2.A, R2.1
unnamed: JP1.3, PHOTODIODE2.K (C), R7.1
unnamed: LED3.A, R3.1
unnamed: JP1.4, PHOTODIODE3.K (C), R8.1
unnamed: LED4.A, R4.1
unnamed: JP1.5, PHOTODIODE4.K (C), R9.1
unnamed: LED5.A, R5.1
unnamed: JP1.6, PHOTODIODE5.K (C), R10.1
unnamed: JP1.1, R1.2, R2.2, R3.2, R4.2, R5.2, R6.2, R7.2, R8.2, R9.2, R10.2
unnamed: JP1.7, LED1.K (C), LED2.K (C), LED3.K (C), LED4.K (C), LED5.K (C), PHOTODIODE1.A, PHOTODIODE2.A, PHOTODIODE3.A, PHOTODIODE4.A, PHOTODIODE5.A
unnamed: JP1.2, PHOTODIODE1.K (C), R6.1

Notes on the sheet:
Copyright S.Goscik 2015. This documentation describes Open Hardware and is licensed under the CERN OHL v. 1.2. You may redistribute and modify this documentation under the terms of the CERN OHL v.1.2. (http://ohwr.org/cernohl). This documentation is distributed WITHOUT ANY EXPRESS OR IMPLIED WARRAN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

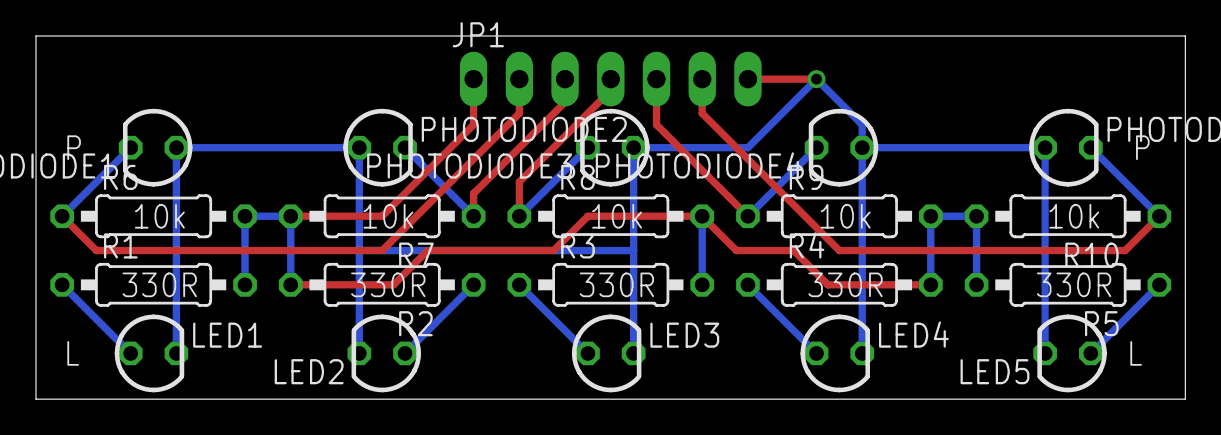
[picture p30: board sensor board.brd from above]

Board: 2 copper layers, 63.9 x 20.2 mm, 21 parts (0 on the bottom side), 12 nets.

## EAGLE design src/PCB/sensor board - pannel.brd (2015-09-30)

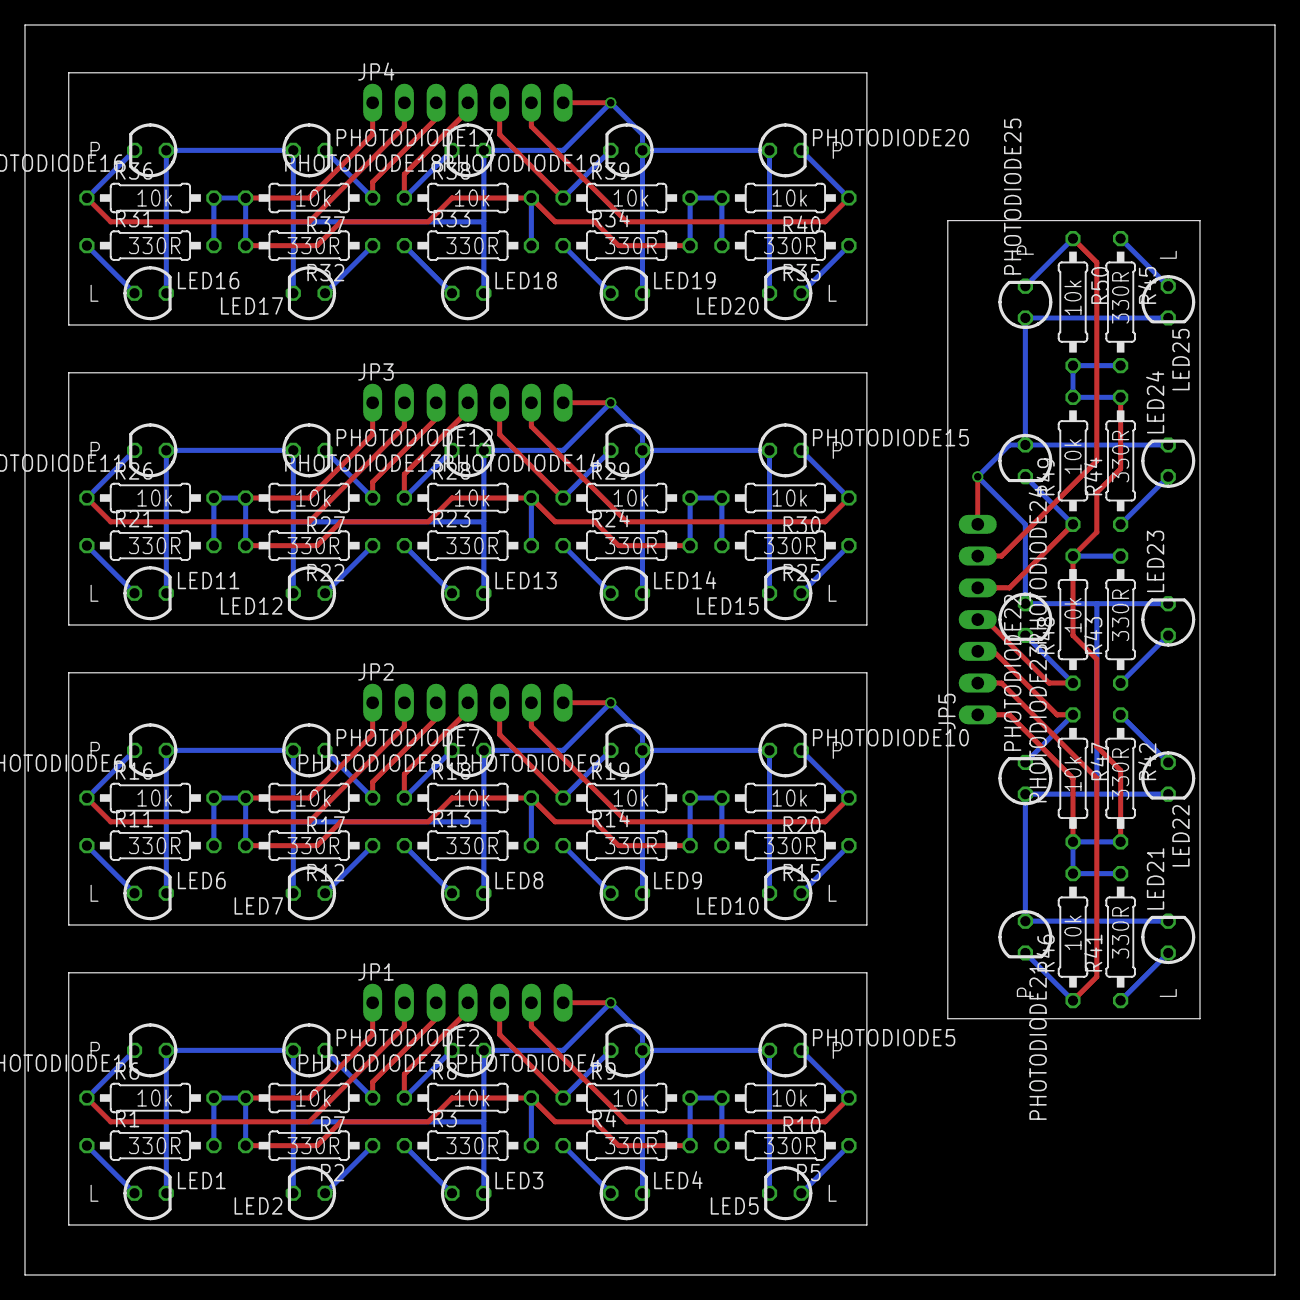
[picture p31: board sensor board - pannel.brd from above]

Board: 4 copper layers, 100.0 x 100.0 mm, 105 parts (0 on the bottom side), 60 nets.

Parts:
JP1, JP2, JP3, JP4, JP5: 1X07
LED1, LED2, LED3, LED4, LED5, LED6, LED7, LED8, LED9, LED10, LED11, LED12, LED13, LED14, LED15, LED16, LED17, LED18, LED19, LED20, LED21, LED22, LED23, LED24, LED25: LED3MM
PHOTODIODE1, PHOTODIODE2, PHOTODIODE3, PHOTODIODE4, PHOTODIODE5, PHOTODIODE6, PHOTODIODE7, PHOTODIODE8, PHOTODIODE9, PHOTODIODE10, PHOTODIODE11, PHOTODIODE12, PHOTODIODE13, PHOTODIODE14, PHOTODIODE15, PHOTODIODE16, PHOTODIODE17, PHOTODIODE18, PHOTODIODE19, PHOTODIODE20, PHOTODIODE21, PHOTODIODE22, PHOTODIODE23, PHOTODIODE24, PHOTODIODE25: LED3MM
R1, R2, R3, R4, R5, R6, R7, R8, R9, R10, R11, R12, R13, R14, R15, R16, R17, R18, R19, R20, R21, R22, R23, R24, R25, R26, R27, R28, R29, R30, R31, R32, R33, R34, R35, R36, R37, R38, R39, R40, R41, R42, R43, R44, R45, R46, R47, R48, R49, R50: 0207/10

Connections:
unnamed: LED1.A, R1.1
unnamed: LED6.A, R11.1
unnamed: LED2.A, R2.1
unnamed: JP1.3, PHOTODIODE2.K, R7.1
unnamed: LED3.A, R3.1
unnamed: JP1.4, PHOTODIODE3.K, R8.1
unnamed: LED4.A, R4.1
unnamed: JP1.5, PHOTODIODE4.K, R9.1
unnamed: LED5.A, R5.1
unnamed: JP1.6, PHOTODIODE5.K, R10.1
unnamed: JP1.1, R1.2, R2.2, R3.2, R4.2, R5.2, R6.2, R7.2, R8.2, R9.2, R10.2
unnamed: JP1.7, LED1.K, LED2.K, LED3.K, LED4.K, LED5.K, PHOTODIODE1.A, PHOTODIODE2.A, PHOTODIODE3.A, PHOTODIODE4.A, PHOTODIODE5.A
unnamed: JP1.2, PHOTODIODE1.K, R6.1
unnamed: LED7.A, R12.1
unnamed: JP2.3, PHOTODIODE7.K, R17.1
unnamed: LED8.A, R13.1
unnamed: JP2.4, PHOTODIODE8.K, R18.1
unnamed: LED9.A, R14.1
unnamed: JP2.5, PHOTODIODE9.K, R19.1
unnamed: LED10.A, R15.1
unnamed: JP2.6, PHOTODIODE10.K, R20.1
unnamed: JP2.1, R11.2, R12.2, R13.2, R14.2, R15.2, R16.2, R17.2, R18.2, R19.2, R20.2
unnamed: JP2.7, LED6.K, LED7.K, LED8.K, LED9.K, LED10.K, PHOTODIODE6.A, PHOTODIODE7.A, PHOTODIODE8.A, PHOTODIODE9.A, PHOTODIODE10.A
unnamed: JP2.2, PHOTODIODE6.K, R16.1
unnamed: LED11.A, R21.1
unnamed: LED12.A, R22.1
unnamed: JP3.3, PHOTODIODE12.K, R27.1
unnamed: LED13.A, R23.1
unnamed: JP3.4, PHOTODIODE13.K, R28.1
unnamed: LED14.A, R24.1
unnamed: JP3.5, PHOTODIODE14.K, R29.1
unnamed: LED15.A, R25.1
unnamed: JP3.6, PHOTODIODE15.K, R30.1
unnamed: JP3.1, R21.2, R22.2, R23.2, R24.2, R25.2, R26.2, R27.2, R28.2, R29.2, R30.2
unnamed: JP3.7, LED11.K, LED12.K, LED13.K, LED14.K, LED15.K, PHOTODIODE11.A, PHOTODIODE12.A, PHOTODIODE13.A, PHOTODIODE14.A, PHOTODIODE15.A
unnamed: JP3.2, PHOTODIODE11.K, R26.1
unnamed: LED16.A, R31.1
unnamed: LED17.A, R32.1
unnamed: JP4.3, PHOTODIODE17.K, R37.1
unnamed: LED18.A, R33.1
unnamed: JP4.4, PHOTODIODE18.K, R38.1
unnamed: LED19.A, R34.1
unnamed: JP4.5, PHOTODIODE19.K, R39.1
unnamed: LED20.A, R35.1
unnamed: JP4.6, PHOTODIODE20.K, R40.1
unnamed: JP4.1, R31.2, R32.2, R33.2, R34.2, R35.2, R36.2, R37.2, R38.2, R39.2, R40.2
unnamed: JP4.7, LED16.K, LED17.K, LED18.K, LED19.K, LED20.K, PHOTODIODE16.A, PHOTODIODE17.A, PHOTODIODE18.A, PHOTODIODE19.A, PHOTODIODE20.A
unnamed: JP4.2, PHOTODIODE16.K, R36.1
unnamed: LED21.A, R41.1
unnamed: LED22.A, R42.1
unnamed: JP5.3, PHOTODIODE22.K, R47.1
unnamed: LED23.A, R43.1
unnamed: JP5.4, PHOTODIODE23.K, R48.1
unnamed: LED24.A, R44.1
unnamed: JP5.5, PHOTODIODE24.K, R49.1
unnamed: LED25.A, R45.1
unnamed: JP5.6, PHOTODIODE25.K, R50.1
unnamed: JP5.1, R41.2, R42.2, R43.2, R44.2, R45.2, R46.2, R47.2, R48.2, R49.2, R50.2
unnamed: JP5.7, LED21.K, LED22.K, LED23.K, LED24.K, LED25.K, PHOTODIODE21.A, PHOTODIODE22.A, PHOTODIODE23.A, PHOTODIODE24.A, PHOTODIODE25.A
unnamed: JP5.2, PHOTODIODE21.K, R46.1

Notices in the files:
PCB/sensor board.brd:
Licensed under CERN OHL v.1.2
